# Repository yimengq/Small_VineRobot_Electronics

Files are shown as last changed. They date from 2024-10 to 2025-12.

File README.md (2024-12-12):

# Board Design for Vine Robot:

## Overview:
### Gen 1 Board:
- Initially split into 4 total boards, 2 on outside for Sensing board + Power Module, and 2 on inside for POE communication board
- The external tip sensing board is designed based on ESP32 XIAO

### Gen 2 Board:
-

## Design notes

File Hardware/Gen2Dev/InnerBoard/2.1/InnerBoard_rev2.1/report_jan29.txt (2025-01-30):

Info: Processing symbol 'C1:Capacitor_SMD:C_0805_2012Metric'.
Info: Processing symbol 'C2:Capacitor_SMD:C_0805_2012Metric'.
Info: Processing symbol 'C3:Capacitor_SMD:C_0805_2012Metric'.
Info: Processing symbol 'C4:Capacitor_SMD:C_0805_2012Metric'.
Info: Processing symbol 'C5:Capacitor_SMD:C_0805_2012Metric'.
Info: Processing symbol 'C6:Capacitor_SMD:C_0805_2012Metric'.
Info: Processing symbol 'C7:Capacitor_SMD:C_0805_2012Metric'.
Info: Processing symbol 'C8:Capacitor_SMD:C_0805_2012Metric'.
Info: Processing symbol 'C20:Capacitor_SMD:C_0805_2012Metric'.
Info: Processing symbol 'C21:Capacitor_SMD:C_0805_2012Metric'.
Info: Processing symbol 'C22:Capacitor_SMD:C_0805_2012Metric'.
Info: Processing symbol 'C23:Capacitor_SMD:C_0805_2012Metric'.
Info: Processing symbol 'C24:Capacitor_SMD:C_0402_1005Metric'.
Info: Processing symbol 'C25:Capacitor_SMD:C_0805_2012Metric'.
Info: Processing symbol 'C26:'.
Info: Processing symbol 'Y3:ASV-50.000MHZ-LCS-T:XTAL_ASV-50.000MHZ-LCS-T'.
Info: Processing symbol 'C27:'.
Info: Processing symbol 'Y1:ABLS2-12.000MHZ-D4Y-T:XTAL_ABLS2-12.000MHZ-D4Y-T'.
Info: Processing symbol 'C29:Capacitor_SMD:C_0402_1005Metric'.
Info: Processing symbol 'C31:Capacitor_SMD:C_0805_2012Metric'.
Info: Processing symbol 'C32:Capacitor_SMD:C_0805_2012Metric'.
Info: Processing symbol 'C59:Capacitor_SMD:C_0805_2012Metric'.
Info: Processing symbol 'C60:Capacitor_SMD:C_0805_2012Metric'.
Info: Processing symbol 'C61:Capacitor_SMD:C_0805_2012Metric'.
Info: Processing symbol 'C62:Capacitor_SMD:C_0805_2012Metric'.
Info: Processing symbol 'C63:Capacitor_SMD:C_0805_2012Metric'.
Info: Processing symbol 'C64:Capacitor_SMD:C_0805_2012Metric'.
Info: Processing symbol 'C65:Capacitor_SMD:C_0805_2012Metric'.
Info: Processing symbol 'C66:Capacitor_SMD:C_0805_2012Metric'.
Info: Processing symbol 'C67:Capacitor_SMD:C_0805_2012Metric'.
Info: Processing symbol 'C68:Capacitor_SMD:C_0805_2012Metric'.
Info: Processing symbol 'C69:Capacitor_SMD:C_0805_2012Metric'.
Info: Processing symbol 'C70:Capacitor_SMD:C_0805_2012Metric'.
Info: Processing symbol 'C71:Capacitor_SMD:C_0805_2012Metric'.
Info: Processing symbol 'C72:Capacitor_SMD:C_0805_2012Metric'.
Info: Processing symbol 'D4:LED_SMD:LED_0603_1608Metric'.
Info: Processing symbol 'D5:LED_SMD:LED_0603_1608Metric'.
Info: Processing symbol 'D6:Diode_THT:D_DO-41_SOD81_P10.16mm_Horizontal'.
Info: Processing symbol 'D7:LED_SMD:LED_0603_1608Metric'.
Info: Processing symbol 'D10:Diode_SMD:D_SOD-323'.
Info: Processing symbol 'D11:LED_SMD:LED_0603_1608Metric'.
Info: Processing symbol 'D13:Diode_SMD:D_SOD-323'.
Info: Processing symbol 'D14:Diode_SMD:D_SOD-323'.
Info: Processing symbol 'D15:Package_TO_SOT_SMD:SOT-23'.
Info: Processing symbol 'D23:Diode_SMD:D_SMA'.
Info: Processing symbol 'D24:Package_TO_SOT_SMD:SOT-23'.
Info: Processing symbol 'FID1:Fiducial:Fiducial_0.5mm_Mask1.5mm'.
Info: Processing symbol 'FID2:Fiducial:Fiducial_0.5mm_Mask1.5mm'.
Info: Processing symbol 'FID3:Fiducial:Fiducial_0.5mm_Mask1.5mm'.
Info: Processing symbol 'FID4:Fiducial:Fiducial_0.5mm_Mask1.5mm'.
Info: Processing symbol 'H1:MountingHole:MountingHole_2.1mm'.
Info: Processing symbol 'H2:MountingHole:MountingHole_2.1mm'.
Info: Processing symbol 'H3:MountingHole:MountingHole_2.1mm'.
Info: Processing symbol 'H4:MountingHole:MountingHole_2.1mm'.
Info: Processing symbol 'J1:HMTSW-102-X-X-S-X:SAMTEC_HMTSW-102-X-X-S-X'.
Info: Processing symbol 'U25:'.
Info: Processing symbol 'J2:HMTSW-102-X-X-S-X:SAMTEC_HMTSW-102-X-X-S-X'.
Info: Processing symbol 'J3:HMTSW-102-X-X-S-X:SAMTEC_HMTSW-102-X-X-S-X'.
Info: Processing symbol 'J4:HMTSW-102-X-X-S-X:SAMTEC_HMTSW-102-X-X-S-X'.
Info: Processing symbol 'J5:UJ31-CH-G2-SMT-TR:CUI_UJ31-CH-G2-SMT-TR'.
Info: Processing symbol 'J6:SI-46020-F:BEL_SI-46020-F'.
Info: Processing symbol 'U23:DBV0005A_N'.
Info: Processing symbol 'J7:HMTSW-102-X-X-S-X:SAMTEC_HMTSW-102-X-X-S-X'.
Info: Processing symbol 'U12:PW8'.
Info: Processing symbol 'J8:CONN10_3221-10-0300-00_CNC'.
Info: Processing symbol 'U11:QFN32_5X5MC_MCH'.
Info: Processing symbol 'J9:HMTSW-102-X-X-S-X:SAMTEC_HMTSW-102-X-X-S-X'.
Info: Processing symbol 'J10:HMTSW-102-X-X-S-X:SAMTEC_HMTSW-102-X-X-S-X'.
Info: Processing symbol 'U10:ESP32_WROOM_32E_N8:ESP32­WROOM­32E_EXP'.
Info: Processing symbol 'J11:HMTSW-102-X-X-S-X:SAMTEC_HMTSW-102-X-X-S-X'.
Info: Processing symbol 'U9:FT232RQ:QFN50P500X500X90-33N'.
Info: Processing symbol 'J12:HMTSW-102-X-X-S-X:SAMTEC_HMTSW-102-X-X-S-X'.
Info: Processing symbol 'U7:Package_TO_SOT_SMD:SOT-223-3_TabPin2'.
Info: Processing symbol 'J13:HMTSW-102-X-X-S-X:SAMTEC_HMTSW-102-X-X-S-X'.
Info: Processing symbol 'U6:Package_TO_SOT_SMD:SOT-23-5'.
Info: Processing symbol 'J14:HMTSW-102-X-X-S-X:SAMTEC_HMTSW-102-X-X-S-X'.
Info: Processing symbol 'U4:Package_TO_SOT_SMD:SOT-23-5'.
Info: Processing symbol 'J15:HMTSW-102-X-X-S-X:SAMTEC_HMTSW-102-X-X-S-X'.
Info: Processing symbol 'U1:DSS0012B'.
Info: Processing symbol 'J16:HMTSW-102-X-X-S-X:SAMTEC_HMTSW-102-X-X-S-X'.
Info: Processing symbol 'TP7:TestPoint:TestPoint_Pad_D2.0mm'.
Info: Processing symbol 'J17:HMTSW-102-X-X-S-X:SAMTEC_HMTSW-102-X-X-S-X'.
Info: Processing symbol 'TP6:TestPoint:TestPoint_Pad_D2.0mm'.
Info: Processing symbol 'J18:HMTSW-102-X-X-S-X:SAMTEC_HMTSW-102-X-X-S-X'.
Info: Processing symbol 'TP5:TestPoint:TestPoint_Pad_D2.0mm'.
Info: Processing symbol 'J19:HMTSW-102-X-X-S-X:SAMTEC_HMTSW-102-X-X-S-X'.
Info: Processing symbol 'TP4:TestPoint:TestPoint_Pad_D2.0mm'.
Info: Processing symbol 'JP1:'.
Info: Processing symbol 'TP3:TestPoint:TestPoint_Pad_D2.0mm'.
Info: Processing symbol 'L8:Inductor_SMD:L_0805_2012Metric'.
Info: Processing symbol 'L9:Inductor_SMD:L_0805_2012Metric'.
Info: Processing symbol 'MH1:OLIMEX_Other-FP:Mounting_hole_Shield_3.3mm'.
Info: Processing symbol 'TP2:TestPoint:TestPoint_Pad_D2.0mm'.
Info: Processing symbol 'MH2:OLIMEX_Other-FP:Mounting_hole_Shield_3.3mm'.
Info: Processing symbol 'TP1:TestPoint:TestPoint_Pad_D2.0mm'.
Info: Processing symbol 'Q1:SI2323DS-T1-GE3:SOT23'.
Info: Processing symbol 'Q4:Package_TO_SOT_SMD:SOT-23'.
Info: Processing symbol 'Q5:Package_TO_SOT_SMD:SOT-23'.
Info: Processing symbol 'Q9:SI2323DS-T1-GE3:SOT23'.
Info: Processing symbol 'Q10:Package_TO_SOT_SMD:SOT-23'.
Info: Processing symbol 'R1:Resistor_SMD:R_0805_2012Metric'.
Info: Processing symbol 'R2:Resistor_SMD:R_0805_2012Metric'.
Info: Processing symbol 'R3:Resistor_SMD:R_0805_2012Metric'.
Info: Processing symbol 'R4:Resistor_SMD:R_0805_2012Metric'.
Info: Processing symbol 'R5:Resistor_SMD:R_0805_2012Metric'.
Info: Processing symbol 'R6:Resistor_SMD:R_0805_2012Metric'.
Info: Processing symbol 'R7:Resistor_SMD:R_0805_2012Metric'.
Info: Processing symbol 'R8:Resistor_SMD:R_0805_2012Metric'.
Info: Processing symbol 'R21:Resistor_SMD:R_0805_2012Metric'.
Info: Processing symbol 'R22:Resistor_SMD:R_0805_2012Metric'.
Info: Processing symbol 'R23:Resistor_SMD:R_0805_2012Metric'.
Info: Processing symbol 'R24:Resistor_SMD:R_0805_2012Metric'.
Info: Processing symbol 'R25:Resistor_SMD:R_0805_2012Metric'.
Info: Processing symbol 'R26:Resistor_SMD:R_0805_2012Metric'.
Info: Processing symbol 'R27:Resistor_SMD:R_0805_2012Metric'.
Info: Processing symbol 'R28:Resistor_SMD:R_0805_2012Metric'.
Info: Processing symbol 'R29:Resistor_SMD:R_0805_2012Metric'.
Info: Processing symbol 'R30:Resistor_SMD:R_0805_2012Metric'.
Info: Processing symbol 'R31:Resistor_SMD:R_0805_2012Metric'.
Info: Processing symbol 'R32:Resistor_SMD:R_0805_2012Metric'.
Info: Processing symbol 'R33:Resistor_SMD:R_0805_2012Metric'.
Info: Processing symbol 'R34:Resistor_SMD:R_0805_2012Metric'.
Info: Processing symbol 'R35:Resistor_SMD:R_0805_2012Metric'.
Info: Processing symbol 'R41:Resistor_SMD:R_0805_2012Metric'.
Info: Processing symbol 'R42:Resistor_SMD:R_0805_2012Metric'.
Info: Processing symbol 'R43:Resistor_SMD:R_0805_2012Metric'.
Info: Processing symbol 'R45:Resistor_SMD:R_0805_2012Metric'.
Info: Processing symbol 'R46:Resistor_SMD:R_0805_2012Metric'.
Info: Processing symbol 'R47:Resistor_SMD:R_0805_2012Metric'.
Info: Processing symbol 'R49:Resistor_SMD:R_0805_2012Metric'.
Info: Processing symbol 'R50:Resistor_SMD:R_0805_2012Metric'.
Info: Processing symbol 'R51:Resistor_SMD:R_0805_2012Metric'.
Info: Processing symbol 'R52:Resistor_SMD:R_0805_2012Metric'.
Info: Processing symbol 'R81:Resistor_SMD:R_0805_2012Metric'.
Info: Processing symbol 'R82:Resistor_SMD:R_0805_2012Metric'.
Info: Processing symbol 'R83:Resistor_SMD:R_0805_2012Metric'.
Info: Processing symbol 'R84:Resistor_SMD:R_0805_2012Metric'.
Info: Processing symbol 'R89:Resistor_SMD:R_0805_2012Metric'.
Info: Processing symbol 'R90:Resistor_SMD:R_0805_2012Metric'.
Info: Processing symbol 'R93:Resistor_SMD:R_0805_2012Metric'.
Info: Processing symbol 'R94:Resistor_SMD:R_0805_2012Metric'.
Info: Processing symbol 'R97:Resistor_SMD:R_0805_2012Metric'.
Info: Processing symbol 'R99:Resistor_SMD:R_0805_2012Metric'.
Info: Processing symbol 'R100:Resistor_SMD:R_0805_2012Metric'.
Info: Processing symbol 'R101:Resistor_SMD:R_0805_2012Metric'.
Info: Processing symbol 'R104:Resistor_SMD:R_0805_2012Metric'.
Info: Processing symbol 'R105:Resistor_SMD:R_0805_2012Metric'.
Info: Processing symbol 'R106:Resistor_SMD:R_0805_2012Metric'.
Info: Processing symbol 'R107:Resistor_SMD:R_0805_2012Metric'.
Info: Processing symbol 'R108:Resistor_SMD:R_0805_2012Metric'.
Info: Processing symbol 'R109:Resistor_SMD:R_0805_2012Metric'.
Info: Processing symbol 'SW1:SW4_PTS815 SJM 250 SMTR LFS_CNK'.
Info: Processing symbol 'SW2:SW4_PTS815 SJM 250 SMTR LFS_CNK'.
Warning: No net found for component U9 pad 23 (no pin 23 in symbol).
Warning: No net found for component J6 pad 8 (no pin 8 in symbol).
Warning: No net found for component U9 pad 5 (no pin 5 in symbol).
Warning: No net found for component U9 pad 12 (no pin 12 in symbol).
Warning: No net found for component U9 pad 25 (no pin 25 in symbol).
Warning: No net found for component U9 pad 29 (no pin 29 in symbol).
Warning: No net found for component U9 pad 13 (no pin 13 in symbol).
Warning: No net found for component U6 pad 1 (no pin 1 in symbol).
Error: Cannot add J16 (footprint 'HMTSW-102-X-X-S-X:SAMTEC_HMTSW-102-X-X-S-X' not found).
Error: Cannot add J15 (footprint 'HMTSW-102-X-X-S-X:SAMTEC_HMTSW-102-X-X-S-X' not found).
Error: Cannot update U1 (footprint 'DSS0012B' not found).
Error: Cannot add J14 (footprint 'HMTSW-102-X-X-S-X:SAMTEC_HMTSW-102-X-X-S-X' not found).
Error: Cannot add J13 (footprint 'HMTSW-102-X-X-S-X:SAMTEC_HMTSW-102-X-X-S-X' not found).
Error: Cannot add J17 (footprint 'HMTSW-102-X-X-S-X:SAMTEC_HMTSW-102-X-X-S-X' not found).
Error: Cannot add J12 (footprint 'HMTSW-102-X-X-S-X:SAMTEC_HMTSW-102-X-X-S-X' not found).
Error: Cannot add J11 (footprint 'HMTSW-102-X-X-S-X:SAMTEC_HMTSW-102-X-X-S-X' not found).
Error: Cannot update SW1 (footprint 'SW4_PTS815 SJM 250 SMTR LFS_CNK' not found).
Error: Cannot add J18 (footprint 'HMTSW-102-X-X-S-X:SAMTEC_HMTSW-102-X-X-S-X' not found).
Error: Cannot add J19 (footprint 'HMTSW-102-X-X-S-X:SAMTEC_HMTSW-102-X-X-S-X' not found).
Error: Cannot add JP1 (no footprint assigned).
Error: Cannot add MH1 (footprint 'OLIMEX_Other-FP:Mounting_hole_Shield_3.3mm' not found).
Error: Cannot add MH2 (footprint 'OLIMEX_Other-FP:Mounting_hole_Shield_3.3mm' not found).
Error: Cannot add J10 (footprint 'HMTSW-102-X-X-S-X:SAMTEC_HMTSW-102-X-X-S-X' not found).
Error: Cannot update J8 (footprint 'CONN10_3221-10-0300-00_CNC' not found).
Error: Cannot update U11 (footprint 'QFN32_5X5MC_MCH' not found).
Error: Cannot add J7 (footprint 'HMTSW-102-X-X-S-X:SAMTEC_HMTSW-102-X-X-S-X' not found).
Error: Cannot update U12 (footprint 'PW8' not found).
Error: Cannot update SW2 (footprint 'SW4_PTS815 SJM 250 SMTR LFS_CNK' not found).
Error: Cannot update U23 (footprint 'DBV0005A_N' not found).
Error: Cannot add J1 (footprint 'HMTSW-102-X-X-S-X:SAMTEC_HMTSW-102-X-X-S-X' not found).
Error: Cannot add U25 (no footprint assigned).
Error: Cannot add C27 (no footprint assigned).
Error: Cannot add C26 (no footprint assigned).

Info: Total warnings: 8, errors: 25.

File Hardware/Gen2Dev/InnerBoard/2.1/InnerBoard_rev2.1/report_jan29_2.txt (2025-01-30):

Info: Processing symbol 'C1:Capacitor_SMD:C_0805_2012Metric'.
Info: Processing symbol 'C2:Capacitor_SMD:C_0805_2012Metric'.
Info: Processing symbol 'C3:Capacitor_SMD:C_0805_2012Metric'.
Info: Processing symbol 'C4:Capacitor_SMD:C_0805_2012Metric'.
Info: Processing symbol 'C5:Capacitor_SMD:C_0805_2012Metric'.
Info: Processing symbol 'C6:Capacitor_SMD:C_0805_2012Metric'.
Info: Processing symbol 'C7:Capacitor_SMD:C_0805_2012Metric'.
Info: Processing symbol 'C8:Capacitor_SMD:C_0805_2012Metric'.
Info: Processing symbol 'C20:Capacitor_SMD:C_0805_2012Metric'.
Info: Processing symbol 'C21:Capacitor_SMD:C_0805_2012Metric'.
Info: Processing symbol 'C22:Capacitor_SMD:C_0805_2012Metric'.
Info: Processing symbol 'C23:Capacitor_SMD:C_0805_2012Metric'.
Info: Processing symbol 'C24:Capacitor_SMD:C_0402_1005Metric'.
Info: Processing symbol 'C25:Capacitor_SMD:C_0805_2012Metric'.
Info: Processing symbol 'C26:'.
Info: Processing symbol 'Y1:ABLS2-12.000MHZ-D4Y-T:XTAL_ABLS2-12.000MHZ-D4Y-T'.
Info: Processing symbol 'C27:'.
Info: Processing symbol 'U25:'.
Info: Processing symbol 'C29:Capacitor_SMD:C_0402_1005Metric'.
Info: Processing symbol 'C31:Capacitor_SMD:C_0805_2012Metric'.
Info: Processing symbol 'C32:Capacitor_SMD:C_0805_2012Metric'.
Info: Processing symbol 'C59:Capacitor_SMD:C_0805_2012Metric'.
Info: Processing symbol 'C60:Capacitor_SMD:C_0805_2012Metric'.
Info: Processing symbol 'C61:Capacitor_SMD:C_0805_2012Metric'.
Info: Processing symbol 'C62:Capacitor_SMD:C_0805_2012Metric'.
Info: Processing symbol 'C63:Capacitor_SMD:C_0805_2012Metric'.
Info: Processing symbol 'C64:Capacitor_SMD:C_0805_2012Metric'.
Info: Processing symbol 'C65:Capacitor_SMD:C_0805_2012Metric'.
Info: Processing symbol 'C66:Capacitor_SMD:C_0805_2012Metric'.
Info: Processing symbol 'C67:Capacitor_SMD:C_0805_2012Metric'.
Info: Processing symbol 'C68:Capacitor_SMD:C_0805_2012Metric'.
Info: Processing symbol 'C69:Capacitor_SMD:C_0805_2012Metric'.
Info: Processing symbol 'C70:Capacitor_SMD:C_0805_2012Metric'.
Info: Processing symbol 'C71:Capacitor_SMD:C_0805_2012Metric'.
Info: Processing symbol 'C72:Capacitor_SMD:C_0805_2012Metric'.
Info: Processing symbol 'D4:LED_SMD:LED_0603_1608Metric'.
Info: Processing symbol 'D5:LED_SMD:LED_0603_1608Metric'.
Info: Processing symbol 'D6:Diode_THT:D_DO-41_SOD81_P10.16mm_Horizontal'.
Info: Processing symbol 'D7:LED_SMD:LED_0603_1608Metric'.
Info: Processing symbol 'D10:Diode_SMD:D_SOD-323'.
Info: Processing symbol 'D11:LED_SMD:LED_0603_1608Metric'.
Info: Processing symbol 'D13:Diode_SMD:D_SOD-323'.
Info: Processing symbol 'D14:Diode_SMD:D_SOD-323'.
Info: Processing symbol 'D15:Package_TO_SOT_SMD:SOT-23'.
Info: Processing symbol 'D23:Diode_SMD:D_SMA'.
Info: Processing symbol 'D24:Package_TO_SOT_SMD:SOT-23'.
Info: Processing symbol 'FID1:Fiducial:Fiducial_0.5mm_Mask1.5mm'.
Info: Processing symbol 'FID2:Fiducial:Fiducial_0.5mm_Mask1.5mm'.
Info: Processing symbol 'FID3:Fiducial:Fiducial_0.5mm_Mask1.5mm'.
Info: Processing symbol 'FID4:Fiducial:Fiducial_0.5mm_Mask1.5mm'.
Info: Processing symbol 'H1:MountingHole:MountingHole_2.1mm'.
Info: Processing symbol 'H2:MountingHole:MountingHole_2.1mm'.
Info: Processing symbol 'H3:MountingHole:MountingHole_2.1mm'.
Info: Processing symbol 'H4:MountingHole:MountingHole_2.1mm'.
Info: Processing symbol 'J1:HMTSW-102-X-X-S-X:SAMTEC_HMTSW-102-X-X-S-X'.
Info: Processing symbol 'U23:DBV0005A_N'.
Info: Processing symbol 'J2:HMTSW-102-X-X-S-X:SAMTEC_HMTSW-102-X-X-S-X'.
Info: Processing symbol 'J3:HMTSW-102-X-X-S-X:SAMTEC_HMTSW-102-X-X-S-X'.
Info: Processing symbol 'J4:HMTSW-102-X-X-S-X:SAMTEC_HMTSW-102-X-X-S-X'.
Info: Processing symbol 'J5:UJ31-CH-G2-SMT-TR:CUI_UJ31-CH-G2-SMT-TR'.
Info: Processing symbol 'J6:SI-46020-F:BEL_SI-46020-F'.
Info: Processing symbol 'U12:PW8'.
Info: Processing symbol 'J7:HMTSW-102-X-X-S-X:SAMTEC_HMTSW-102-X-X-S-X'.
Info: Processing symbol 'U11:QFN32_5X5MC_MCH'.
Info: Processing symbol 'J8:CONN10_3221-10-0300-00_CNC'.
Info: Processing symbol 'U10:ESP32_WROOM_32E_N8:ESP32­WROOM­32E_EXP'.
Info: Processing symbol 'J9:HMTSW-102-X-X-S-X:SAMTEC_HMTSW-102-X-X-S-X'.
Info: Processing symbol 'J10:HMTSW-102-X-X-S-X:SAMTEC_HMTSW-102-X-X-S-X'.
Info: Processing symbol 'U9:FT232RQ:QFN50P500X500X90-33N'.
Info: Processing symbol 'J11:HMTSW-102-X-X-S-X:SAMTEC_HMTSW-102-X-X-S-X'.
Info: Processing symbol 'U7:Package_TO_SOT_SMD:SOT-223-3_TabPin2'.
Info: Processing symbol 'J12:HMTSW-102-X-X-S-X:SAMTEC_HMTSW-102-X-X-S-X'.
Info: Processing symbol 'U6:Package_TO_SOT_SMD:SOT-23-5'.
Info: Processing symbol 'J13:HMTSW-102-X-X-S-X:SAMTEC_HMTSW-102-X-X-S-X'.
Info: Processing symbol 'U4:Package_TO_SOT_SMD:SOT-23-5'.
Info: Processing symbol 'J14:HMTSW-102-X-X-S-X:SAMTEC_HMTSW-102-X-X-S-X'.
Info: Processing symbol 'U1:DSS0012B'.
Info: Processing symbol 'J15:HMTSW-102-X-X-S-X:SAMTEC_HMTSW-102-X-X-S-X'.
Info: Processing symbol 'TP30:TestPoint:TestPoint_Pad_D2.0mm'.
Info: Processing symbol 'J16:HMTSW-102-X-X-S-X:SAMTEC_HMTSW-102-X-X-S-X'.
Info: Processing symbol 'TP29:TestPoint:TestPoint_Pad_D2.0mm'.
Info: Processing symbol 'J17:HMTSW-102-X-X-S-X:SAMTEC_HMTSW-102-X-X-S-X'.
Info: Processing symbol 'TP28:TestPoint:TestPoint_Pad_D2.0mm'.
Info: Processing symbol 'J18:HMTSW-102-X-X-S-X:SAMTEC_HMTSW-102-X-X-S-X'.
Info: Processing symbol 'TP27:TestPoint:TestPoint_Pad_D2.0mm'.
Info: Processing symbol 'J19:HMTSW-102-X-X-S-X:SAMTEC_HMTSW-102-X-X-S-X'.
Info: Processing symbol 'TP26:TestPoint:TestPoint_Pad_D2.0mm'.
Info: Processing symbol 'JP1:'.
Info: Processing symbol 'TP25:TestPoint:TestPoint_Pad_D2.0mm'.
Info: Processing symbol 'L8:Inductor_SMD:L_0805_2012Metric'.
Info: Processing symbol 'L9:Inductor_SMD:L_0805_2012Metric'.
Info: Processing symbol 'MH1:OLIMEX_Other-FP:Mounting_hole_Shield_3.3mm'.
Info: Processing symbol 'TP24:TestPoint:TestPoint_Pad_D2.0mm'.
Info: Processing symbol 'MH2:OLIMEX_Other-FP:Mounting_hole_Shield_3.3mm'.
Info: Processing symbol 'TP23:TestPoint:TestPoint_Pad_D2.0mm'.
Info: Processing symbol 'Q1:SI2323DS-T1-GE3:SOT23'.
Info: Processing symbol 'Q4:Package_TO_SOT_SMD:SOT-23'.
Info: Processing symbol 'Q5:Package_TO_SOT_SMD:SOT-23'.
Info: Processing symbol 'Q9:SI2323DS-T1-GE3:SOT23'.
Info: Processing symbol 'Q10:Package_TO_SOT_SMD:SOT-23'.
Info: Processing symbol 'R1:Resistor_SMD:R_0805_2012Metric'.
Info: Processing symbol 'R2:Resistor_SMD:R_0805_2012Metric'.
Info: Processing symbol 'R3:Resistor_SMD:R_0805_2012Metric'.
Info: Processing symbol 'R4:Resistor_SMD:R_0805_2012Metric'.
Info: Processing symbol 'R5:Resistor_SMD:R_0805_2012Metric'.
Info: Processing symbol 'R6:Resistor_SMD:R_0805_2012Metric'.
Info: Processing symbol 'R7:Resistor_SMD:R_0805_2012Metric'.
Info: Processing symbol 'R8:Resistor_SMD:R_0805_2012Metric'.
Info: Processing symbol 'R21:Resistor_SMD:R_0805_2012Metric'.
Info: Processing symbol 'R22:Resistor_SMD:R_0805_2012Metric'.
Info: Processing symbol 'R23:Resistor_SMD:R_0805_2012Metric'.
Info: Processing symbol 'R24:Resistor_SMD:R_0805_2012Metric'.
Info: Processing symbol 'R25:Resistor_SMD:R_0805_2012Metric'.
Info: Processing symbol 'R26:Resistor_SMD:R_0805_2012Metric'.
Info: Processing symbol 'R27:Resistor_SMD:R_0805_2012Metric'.
Info: Processing symbol 'R28:Resistor_SMD:R_0805_2012Metric'.
Info: Processing symbol 'R29:Resistor_SMD:R_0805_2012Metric'.
Info: Processing symbol 'R30:Resistor_SMD:R_0805_2012Metric'.
Info: Processing symbol 'R31:Resistor_SMD:R_0805_2012Metric'.
Info: Processing symbol 'R32:Resistor_SMD:R_0805_2012Metric'.
Info: Processing symbol 'R33:Resistor_SMD:R_0805_2012Metric'.
Info: Processing symbol 'R34:Resistor_SMD:R_0805_2012Metric'.
Info: Processing symbol 'R35:Resistor_SMD:R_0805_2012Metric'.
Info: Processing symbol 'R41:Resistor_SMD:R_0805_2012Metric'.
Info: Processing symbol 'R42:Resistor_SMD:R_0805_2012Metric'.
Info: Processing symbol 'R43:Resistor_SMD:R_0805_2012Metric'.
Info: Processing symbol 'R45:Resistor_SMD:R_0805_2012Metric'.
Info: Processing symbol 'R46:Resistor_SMD:R_0805_2012Metric'.
Info: Processing symbol 'R47:Resistor_SMD:R_0805_2012Metric'.
Info: Processing symbol 'R49:Resistor_SMD:R_0805_2012Metric'.
Info: Processing symbol 'R50:Resistor_SMD:R_0805_2012Metric'.
Info: Processing symbol 'R51:Resistor_SMD:R_0805_2012Metric'.
Info: Processing symbol 'R52:Resistor_SMD:R_0805_2012Metric'.
Info: Processing symbol 'R81:Resistor_SMD:R_0805_2012Metric'.
Info: Processing symbol 'R82:Resistor_SMD:R_0805_2012Metric'.
Info: Processing symbol 'R83:Resistor_SMD:R_0805_2012Metric'.
Info: Processing symbol 'R84:Resistor_SMD:R_0805_2012Metric'.
Info: Processing symbol 'R89:Resistor_SMD:R_0805_2012Metric'.
Info: Processing symbol 'R90:Resistor_SMD:R_0805_2012Metric'.
Info: Processing symbol 'R93:Resistor_SMD:R_0805_2012Metric'.
Info: Processing symbol 'R94:Resistor_SMD:R_0805_2012Metric'.
Info: Processing symbol 'R97:Resistor_SMD:R_0805_2012Metric'.
Info: Processing symbol 'R99:Resistor_SMD:R_0805_2012Metric'.
Info: Processing symbol 'R100:Resistor_SMD:R_0805_2012Metric'.
Info: Processing symbol 'R101:Resistor_SMD:R_0805_2012Metric'.
Info: Processing symbol 'R104:Resistor_SMD:R_0805_2012Metric'.
Info: Processing symbol 'R105:Resistor_SMD:R_0805_2012Metric'.
Info: Processing symbol 'R106:Resistor_SMD:R_0805_2012Metric'.
Info: Processing symbol 'R107:Resistor_SMD:R_0805_2012Metric'.
Info: Processing symbol 'R108:Resistor_SMD:R_0805_2012Metric'.
Info: Processing symbol 'R109:Resistor_SMD:R_0805_2012Metric'.
Info: Processing symbol 'SW1:SW4_PTS815 SJM 250 SMTR LFS_CNK'.
Info: Processing symbol 'TP22:TestPoint:TestPoint_Pad_D2.0mm'.
Info: Processing symbol 'SW2:SW4_PTS815 SJM 250 SMTR LFS_CNK'.
Info: Processing symbol 'TP21:TestPoint:TestPoint_Pad_D2.0mm'.
Info: Processing symbol 'TP1:TestPoint:TestPoint_Pad_D2.0mm'.
Info: Processing symbol 'TP2:TestPoint:TestPoint_Pad_D2.0mm'.
Info: Processing symbol 'TP3:TestPoint:TestPoint_Pad_D2.0mm'.
Info: Processing symbol 'TP4:TestPoint:TestPoint_Pad_D2.0mm'.
Info: Processing symbol 'TP5:TestPoint:TestPoint_Pad_D2.0mm'.
Info: Processing symbol 'TP6:TestPoint:TestPoint_Pad_D2.0mm'.
Info: Processing symbol 'TP8:TestPoint:TestPoint_Pad_D2.0mm'.
Info: Processing symbol 'TP20:TestPoint:TestPoint_Pad_D2.0mm'.
Info: Processing symbol 'TP19:TestPoint:TestPoint_Pad_D2.0mm'.
Info: Processing symbol 'TP18:TestPoint:TestPoint_Pad_D2.0mm'.
Info: Processing symbol 'TP17:TestPoint:TestPoint_Pad_D2.0mm'.
Info: Processing symbol 'TP16:TestPoint:TestPoint_Pad_D2.0mm'.
Info: Processing symbol 'TP15:TestPoint:TestPoint_Pad_D2.0mm'.
Info: Processing symbol 'TP14:TestPoint:TestPoint_Pad_D2.0mm'.
Info: Processing symbol 'TP13:TestPoint:TestPoint_Pad_D2.0mm'.
Info: Processing symbol 'Y3:ASV-50.000MHZ-LCS-T:XTAL_ASV-50.000MHZ-LCS-T'.
Info: Processing symbol 'TP9:TestPoint:TestPoint_Pad_D2.0mm'.
Info: Processing symbol 'TP12:TestPoint:TestPoint_Pad_D2.0mm'.
Info: Processing symbol 'TP11:TestPoint:TestPoint_Pad_D2.0mm'.
Info: Processing symbol 'TP10:TestPoint:TestPoint_Pad_D2.0mm'.
Updated TP9 symbol association from  to /6baada33-aa96-4fe6-9113-43f1f558f684.
Updated TP9 sheetname to 'Root'.
Updated TP9 sheetfile to 'InnerBoard_rev2.1.kicad_sch'.
Updated TP9 footprint filters to 'Pin* Test*'.
Removed TP9 'exclude from BOM' fabrication attribute.
Connected TP9 pin 1 to Net-(C71-Pad2).
Changed TP9 value from TestPoint_Pad_D2.0mm to TestPoint.
Added TP10 (footprint 'TestPoint:TestPoint_Pad_D2.0mm').
Changed REF** reference designator to TP10.
Changed TP10 value from TestPoint_Pad_D2.0mm to TestPoint.
Updated TP10 symbol association from  to /1567f1c0-5a2b-43b6-96a9-7105be66c10c.
Updated TP10 sheetname to 'Root'.
Updated TP10 sheetfile to 'InnerBoard_rev2.1.kicad_sch'.
Updated TP10 footprint filters to 'Pin* Test*'.
Removed TP10 'exclude from BOM' fabrication attribute.
Connected TP10 pin 1 to Spare2.
Changed REF** reference designator to TP9.
Added TP11 (footprint 'TestPoint:TestPoint_Pad_D2.0mm').
Changed REF** reference designator to TP11.
Changed TP11 value from TestPoint_Pad_D2.0mm to TestPoint.
Updated TP11 symbol association from  to /7062de12-79e4-4118-8f8d-67129581fe5f.
Updated TP11 sheetname to 'Root'.
Updated TP11 sheetfile to 'InnerBoard_rev2.1.kicad_sch'.
Updated TP11 footprint filters to 'Pin* Test*'.
Removed TP11 'exclude from BOM' fabrication attribute.
Connected TP11 pin 1 to Spare1.
Added TP9 (footprint 'TestPoint:TestPoint_Pad_D2.0mm').
Added TP12 (footprint 'TestPoint:TestPoint_Pad_D2.0mm').
Changed REF** reference designator to TP12.
Changed TP12 value from TestPoint_Pad_D2.0mm to TestPoint.
Updated TP12 symbol association from  to /c7cb2f0c-1bdc-45d0-a05b-4f7ba0fc8c7b.
Updated TP12 sheetname to 'Root'.
Connected TP8 pin 1 to OSC_DIS.
Updated TP12 footprint filters to 'Pin* Test*'.
Removed TP12 'exclude from BOM' fabrication attribute.
Connected TP12 pin 1 to Net-(U11-EPAD).
Removed TP8 'exclude from BOM' fabrication attribute.
Added TP13 (footprint 'TestPoint:TestPoint_Pad_D2.0mm').
Changed REF** reference designator to TP13.
Changed TP13 value from TestPoint_Pad_D2.0mm to TestPoint.
Updated TP13 symbol association from  to /bcef1eed-9b2b-4c54-8e5d-db2f056f6c87.
Updated TP13 sheetname to 'Root'.
Updated TP13 sheetfile to 'InnerBoard_rev2.1.kicad_sch'.
Updated TP13 footprint filters to 'Pin* Test*'.
Removed TP13 'exclude from BOM' fabrication attribute.
Connected TP13 pin 1 to D_Com.
Updated TP8 footprint filters to 'Pin* Test*'.
Added TP14 (footprint 'TestPoint:TestPoint_Pad_D2.0mm').
Changed REF** reference designator to TP14.
Changed TP14 value from TestPoint_Pad_D2.0mm to TestPoint.
Updated TP14 symbol association from  to /e5ea63ed-f4e0-403f-a414-85737eb8aaad.
Updated TP14 sheetname to 'Root'.
Updated TP14 sheetfile to 'InnerBoard_rev2.1.kicad_sch'.
Updated TP14 footprint filters to 'Pin* Test*'.
Removed TP14 'exclude from BOM' fabrication attribute.
Connected TP14 pin 1 to VDDA1/2.
Updated TP8 sheetfile to 'InnerBoard_rev2.1.kicad_sch'.
Added TP15 (footprint 'TestPoint:TestPoint_Pad_D2.0mm').
Changed REF** reference designator to TP15.
Changed TP15 value from TestPoint_Pad_D2.0mm to TestPoint.
Updated TP15 symbol association from  to /d527ba62-d9ac-45c6-8199-df9451cb6658.
Updated TP15 sheetname to 'Root'.
Updated TP15 sheetfile to 'InnerBoard_rev2.1.kicad_sch'.
Updated TP15 footprint filters to 'Pin* Test*'.
Removed TP15 'exclude from BOM' fabrication attribute.
Connected TP15 pin 1 to ESP_EN.
Updated TP8 sheetname to 'Root'.
Added TP16 (footprint 'TestPoint:TestPoint_Pad_D2.0mm').
Changed REF** reference designator to TP16.
Changed TP16 value from TestPoint_Pad_D2.0mm to TestPoint.
Updated TP16 symbol association from  to /d1f3ed2d-daec-4c6f-8942-47c1e0745468.
Updated TP16 sheetname to 'Root'.
Updated TP16 sheetfile to 'InnerBoard_rev2.1.kicad_sch'.
Updated TP16 footprint filters to 'Pin* Test*'.
Removed TP16 'exclude from BOM' fabrication attribute.
Connected TP16 pin 1 to +3.3VLAN.
Updated TP8 symbol association from  to /023d3b54-558e-41d1-8a4c-ee0ba2b6aaef.
Added TP17 (footprint 'TestPoint:TestPoint_Pad_D2.0mm').
Changed REF** reference designator to TP17.
Changed TP17 value from TestPoint_Pad_D2.0mm to TestPoint.
Updated TP17 symbol association from  to /6c0a5c35-ba72-4d07-862e-1288580fff16.
Updated TP17 sheetname to 'Root'.
Updated TP17 sheetfile to 'InnerBoard_rev2.1.kicad_sch'.
Updated TP17 footprint filters to 'Pin* Test*'.
Removed TP17 'exclude from BOM' fabrication attribute.
Connected TP17 pin 1 to Spare2.
Changed TP8 value from TestPoint_Pad_D2.0mm to TestPoint.
Added TP18 (footprint 'TestPoint:TestPoint_Pad_D2.0mm').
Changed REF** reference designator to TP18.
Changed TP18 value from TestPoint_Pad_D2.0mm to TestPoint.
Updated TP18 symbol association from  to /b75fff0e-efaa-4a0c-94cb-2920aa34688c.
Updated TP18 sheetname to 'Root'.
Updated TP18 sheetfile to 'InnerBoard_rev2.1.kicad_sch'.
Updated TP18 footprint filters to 'Pin* Test*'.
Removed TP18 'exclude from BOM' fabrication attribute.
Connected TP18 pin 1 to Net-(U12-UVLO).
Changed REF** reference designator to TP8.
Added TP19 (footprint 'TestPoint:TestPoint_Pad_D2.0mm').
Changed REF** reference designator to TP19.
Changed TP19 value from TestPoint_Pad_D2.0mm to TestPoint.
Updated TP19 symbol association from  to /e3ad6083-1446-41eb-9340-d69c70b52fe2.
Updated TP19 sheetname to 'Root'.
Updated TP19 sheetfile to 'InnerBoard_rev2.1.kicad_sch'.
Updated TP19 footprint filters to 'Pin* Test*'.
Removed TP19 'exclude from BOM' fabrication attribute.
Connected TP19 pin 1 to +5VP.
Added TP8 (footprint 'TestPoint:TestPoint_Pad_D2.0mm').
Added TP20 (footprint 'TestPoint:TestPoint_Pad_D2.0mm').
Changed REF** reference designator to TP20.
Changed TP20 value from TestPoint_Pad_D2.0mm to TestPoint.
Updated TP20 symbol association from  to /f5299f5d-6878-4394-902a-5c750fa8e632.
Updated TP20 sheetname to 'Root'.
Updated TP20 sheetfile to 'InnerBoard_rev2.1.kicad_sch'.
Updated TP20 footprint filters to 'Pin* Test*'.
Removed TP20 'exclude from BOM' fabrication attribute.
Connected TP20 pin 1 to VBUS.
Updated TP12 sheetfile to 'InnerBoard_rev2.1.kicad_sch'.
Added TP21 (footprint 'TestPoint:TestPoint_Pad_D2.0mm').
Changed REF** reference designator to TP21.
Changed TP21 value from TestPoint_Pad_D2.0mm to TestPoint.
Updated TP21 symbol association from  to /23b50038-7e48-425d-869d-8ebaa74cc40e.
Updated TP21 sheetname to 'Root'.
Updated TP21 sheetfile to 'InnerBoard_rev2.1.kicad_sch'.
Updated TP21 footprint filters to 'Pin* Test*'.
Removed TP21 'exclude from BOM' fabrication attribute.
Connected TP21 pin 1 to +5V.
Connected TP30 pin 1 to GPIO5/SPI_CS.
Added TP22 (footprint 'TestPoint:TestPoint_Pad_D2.0mm').
Changed REF** reference designator to TP22.
Changed TP22 value from TestPoint_Pad_D2.0mm to TestPoint.
Updated TP22 symbol association from  to /d2a7ec64-73a1-4d8d-a047-477f0932a324.
Updated TP22 sheetname to 'Root'.
Updated TP22 sheetfile to 'InnerBoard_rev2.1.kicad_sch'.
Updated TP22 footprint filters to 'Pin* Test*'.
Removed TP22 'exclude from BOM' fabrication attribute.
Connected TP22 pin 1 to +9V.
Removed TP30 'exclude from BOM' fabrication attribute.
Added TP23 (footprint 'TestPoint:TestPoint_Pad_D2.0mm').
Changed REF** reference designator to TP23.
Changed TP23 value from TestPoint_Pad_D2.0mm to TestPoint.
Updated TP23 symbol association from  to /2898ca49-4c4a-4b33-8b86-257164c50673.
Updated TP23 sheetname to 'Root'.
Updated TP23 sheetfile to 'InnerBoard_rev2.1.kicad_sch'.
Updated TP23 footprint filters to 'Pin* Test*'.
Removed TP23 'exclude from BOM' fabrication attribute.
Connected TP23 pin 1 to +3.3V.
Updated TP30 footprint filters to 'Pin* Test*'.
Added TP24 (footprint 'TestPoint:TestPoint_Pad_D2.0mm').
Changed REF** reference designator to TP24.
Changed TP24 value from TestPoint_Pad_D2.0mm to TestPoint.
Updated TP24 symbol association from  to /db690d6d-3832-4922-8787-71b01d960507.
Updated TP24 sheetname to 'Root'.
Updated TP24 sheetfile to 'InnerBoard_rev2.1.kicad_sch'.
Updated TP24 footprint filters to 'Pin* Test*'.
Removed TP24 'exclude from BOM' fabrication attribute.
Connected TP24 pin 1 to RMIISEL.
Updated TP30 sheetfile to 'InnerBoard_rev2.1.kicad_sch'.
Added TP25 (footprint 'TestPoint:TestPoint_Pad_D2.0mm').
Changed REF** reference designator to TP25.
Changed TP25 value from TestPoint_Pad_D2.0mm to TestPoint.
Updated TP25 symbol association from  to /ea5cd51e-44af-4205-83e0-52a23ab58acc.
Updated TP25 sheetname to 'Root'.
Updated TP25 sheetfile to 'InnerBoard_rev2.1.kicad_sch'.
Updated TP25 footprint filters to 'Pin* Test*'.
Removed TP25 'exclude from BOM' fabrication attribute.
Connected TP25 pin 1 to Net-(U25-VDD).
Updated TP30 sheetname to 'Root'.
Added TP26 (footprint 'TestPoint:TestPoint_Pad_D2.0mm').
Changed REF** reference designator to TP26.
Changed TP26 value from TestPoint_Pad_D2.0mm to TestPoint.
Updated TP26 symbol association from  to /f6c930f7-10bf-4e56-a248-4fd9497e862e.
Updated TP26 sheetname to 'Root'.
Updated TP26 sheetfile to 'InnerBoard_rev2.1.kicad_sch'.
Updated TP26 footprint filters to 'Pin* Test*'.
Removed TP26 'exclude from BOM' fabrication attribute.
Connected TP26 pin 1 to GPIO12/PHY_PWR.
Updated TP30 symbol association from  to /597af5c2-880d-4a95-b62b-8e9e5aa765af.
Added TP27 (footprint 'TestPoint:TestPoint_Pad_D2.0mm').
Changed REF** reference designator to TP27.
Changed TP27 value from TestPoint_Pad_D2.0mm to TestPoint.
Updated TP27 symbol association from  to /2d84ceed-f113-43e0-9ed7-c3a5eb137c14.
Updated TP27 sheetname to 'Root'.
Updated TP27 sheetfile to 'InnerBoard_rev2.1.kicad_sch'.
Updated TP27 footprint filters to 'Pin* Test*'.
Removed TP27 'exclude from BOM' fabrication attribute.
Connected TP27 pin 1 to GPIO15/HS2_CMD.
Changed TP30 value from TestPoint_Pad_D2.0mm to TestPoint.
Added TP28 (footprint 'TestPoint:TestPoint_Pad_D2.0mm').
Changed REF** reference designator to TP28.
Changed TP28 value from TestPoint_Pad_D2.0mm to TestPoint.
Updated TP28 symbol association from  to /e172e45f-28b6-43ed-a104-899f7bb8fd20.
Updated TP28 sheetname to 'Root'.
Updated TP28 sheetfile to 'InnerBoard_rev2.1.kicad_sch'.
Updated TP28 footprint filters to 'Pin* Test*'.
Removed TP28 'exclude from BOM' fabrication attribute.
Connected TP28 pin 1 to GPIO2/HS2_DATA0.
Changed REF** reference designator to TP30.
Added TP29 (footprint 'TestPoint:TestPoint_Pad_D2.0mm').
Changed REF** reference designator to TP29.
Changed TP29 value from TestPoint_Pad_D2.0mm to TestPoint.
Updated TP29 symbol association from  to /03b79476-c9ff-44dc-b22a-21540050c368.
Updated TP29 sheetname to 'Root'.
Updated TP29 sheetfile to 'InnerBoard_rev2.1.kicad_sch'.
Updated TP29 footprint filters to 'Pin* Test*'.
Removed TP29 'exclude from BOM' fabrication attribute.
Connected TP29 pin 1 to GPIO0.
Added TP30 (footprint 'TestPoint:TestPoint_Pad_D2.0mm').
Warning: No net found for component U9 pad 23 (no pin 23 in symbol).
Warning: No net found for component J6 pad 8 (no pin 8 in symbol).
Warning: No net found for component U9 pad 5 (no pin 5 in symbol).
Warning: No net found for component U9 pad 12 (no pin 12 in symbol).
Warning: No net found for component U9 pad 25 (no pin 25 in symbol).
Warning: No net found for component U9 pad 29 (no pin 29 in symbol).
Warning: No net found for component U9 pad 13 (no pin 13 in symbol).
Warning: No net found for component U6 pad 1 (no pin 1 in symbol).
Error: Cannot update SW1 (footprint 'SW4_PTS815 SJM 250 SMTR LFS_CNK' not found).
Error: Cannot add J14 (footprint 'HMTSW-102-X-X-S-X:SAMTEC_HMTSW-102-X-X-S-X' not found).
Error: Cannot update U1 (footprint 'DSS0012B' not found).
Error: Cannot add J13 (footprint 'HMTSW-102-X-X-S-X:SAMTEC_HMTSW-102-X-X-S-X' not found).
Error: Cannot add J12 (footprint 'HMTSW-102-X-X-S-X:SAMTEC_HMTSW-102-X-X-S-X' not found).
Error: Cannot add MH2 (footprint 'OLIMEX_Other-FP:Mounting_hole_Shield_3.3mm' not found).
Error: Cannot add J11 (footprint 'HMTSW-102-X-X-S-X:SAMTEC_HMTSW-102-X-X-S-X' not found).
Error: Cannot add J10 (footprint 'HMTSW-102-X-X-S-X:SAMTEC_HMTSW-102-X-X-S-X' not found).
Error: Cannot add J15 (footprint 'HMTSW-102-X-X-S-X:SAMTEC_HMTSW-102-X-X-S-X' not found).
Error: Cannot add MH1 (footprint 'OLIMEX_Other-FP:Mounting_hole_Shield_3.3mm' not found).
Error: Cannot add JP1 (no footprint assigned).
Error: Cannot add J19 (footprint 'HMTSW-102-X-X-S-X:SAMTEC_HMTSW-102-X-X-S-X' not found).
Error: Cannot add J18 (footprint 'HMTSW-102-X-X-S-X:SAMTEC_HMTSW-102-X-X-S-X' not found).
Error: Cannot add J17 (footprint 'HMTSW-102-X-X-S-X:SAMTEC_HMTSW-102-X-X-S-X' not found).
Error: Cannot update J8 (footprint 'CONN10_3221-10-0300-00_CNC' not found).
Error: Cannot add J7 (footprint 'HMTSW-102-X-X-S-X:SAMTEC_HMTSW-102-X-X-S-X' not found).
Error: Cannot update U11 (footprint 'QFN32_5X5MC_MCH' not found).
Error: Cannot add J16 (footprint 'HMTSW-102-X-X-S-X:SAMTEC_HMTSW-102-X-X-S-X' not found).
Error: Cannot update U12 (footprint 'PW8' not found).
Error: Cannot add J1 (footprint 'HMTSW-102-X-X-S-X:SAMTEC_HMTSW-102-X-X-S-X' not found).
Error: Cannot update U23 (footprint 'DBV0005A_N' not found).
Error: Cannot add C27 (no footprint assigned).
Error: Cannot add U25 (no footprint assigned).
Error: Cannot add C26 (no footprint assigned).
Error: Cannot update SW2 (footprint 'SW4_PTS815 SJM 250 SMTR LFS_CNK' not found).

Info: Total warnings: 8, errors: 25.

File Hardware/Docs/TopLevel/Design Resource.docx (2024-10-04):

Electronics System Outside

1. Power
  a. Lipo battery
    i. Feature
      1. Multiple cells connected in series.
      2. Current Requirements
        a. Continuous: [Enter value]
        b. Peak: [Enter value] +150mA (motor)
        c. Battery Operating Time: [Enter value]
    ii. Resources
      1. Purchase (https://nassaunationalcable.com/collections/grepow-lipo-round-shaped-batteries/products/grepow-580mah-3-7v-lipo-round-shaped-battery-5535035)
      2. Datasheet
  b. Voltage Converter
    i. Feature
      1. An IC convert voltage from 7.4V to 3.7V
  c. Protection Circuit
    i. Feature
      1. Reverse Polarity Protection
      2. Decoupling Capactiros
      3. EMI/ESD Protection
2. Micros + Sensor Peripheral
  a. ESP32-S3 (XIAO Seeed Studio)
    i. Resource
      1. Dev Board Purchase (https://www.amazon.com/Seeed-Studio-XIAO-ESP32C3-Microcontroller/dp/B0B94JZ2YF?sp_csd=d2lkZ2V0TmFtZT1zcF9hdGY)
      2. Schematic (https://github.com/yimengq/Small_VineRobot_Electronics/tree/main/Example_Schematics/XIAO%20Seeed%20Studio)
      3. Github (https://github.com/yimengq/Small_VineRobot_Electronics/tree/main/Example_Schematics/XIAO%20Seeed%20Studio)
      4. Official Website (https://wiki.seeedstudio.com/xiao_esp32s3_getting_started/)
  b. OV2640
  c. BNO055
    i. Feature: This is 9-axis IMU reused from Adafruit product
    ii. Resource
      1. Dev Board Purchase (https://www.adafruit.com/product/2472)
      2. Schematic (https://learn.adafruit.com/adafruit-bno055-absolute-orientation-sensor/downloads)
      3. Github (https://github.com/yimengq/Small_VineRobot_Electronics/tree/main/Example_Schematics/BNO055)

Electronics System Inside

1. Power
  a. ESP-PoE
    i. Feature
      1. 48V/30W,60W,90W
      2. Ethernet for data communication
    ii. Resources
      1. Dev Board Purchase (https://www.olimex.com/Products/IoT/ESP32/ESP32-POE/open-source-hardware)
      2. Schematic (https://github.com/yimengq/Small_VineRobot_Electronics/blob/main/Example_Schematics/ESP32_POE/Oilmex%20Board/ESP32-PoE_Rev_L1.pdf)
      3. Github (https://github.com/yimengq/Small_VineRobot_Electronics/tree/main/Example_Schematics/ESP32_POE/Oilmex%20Board)
2. Micros
  a. ESP32-WROOM

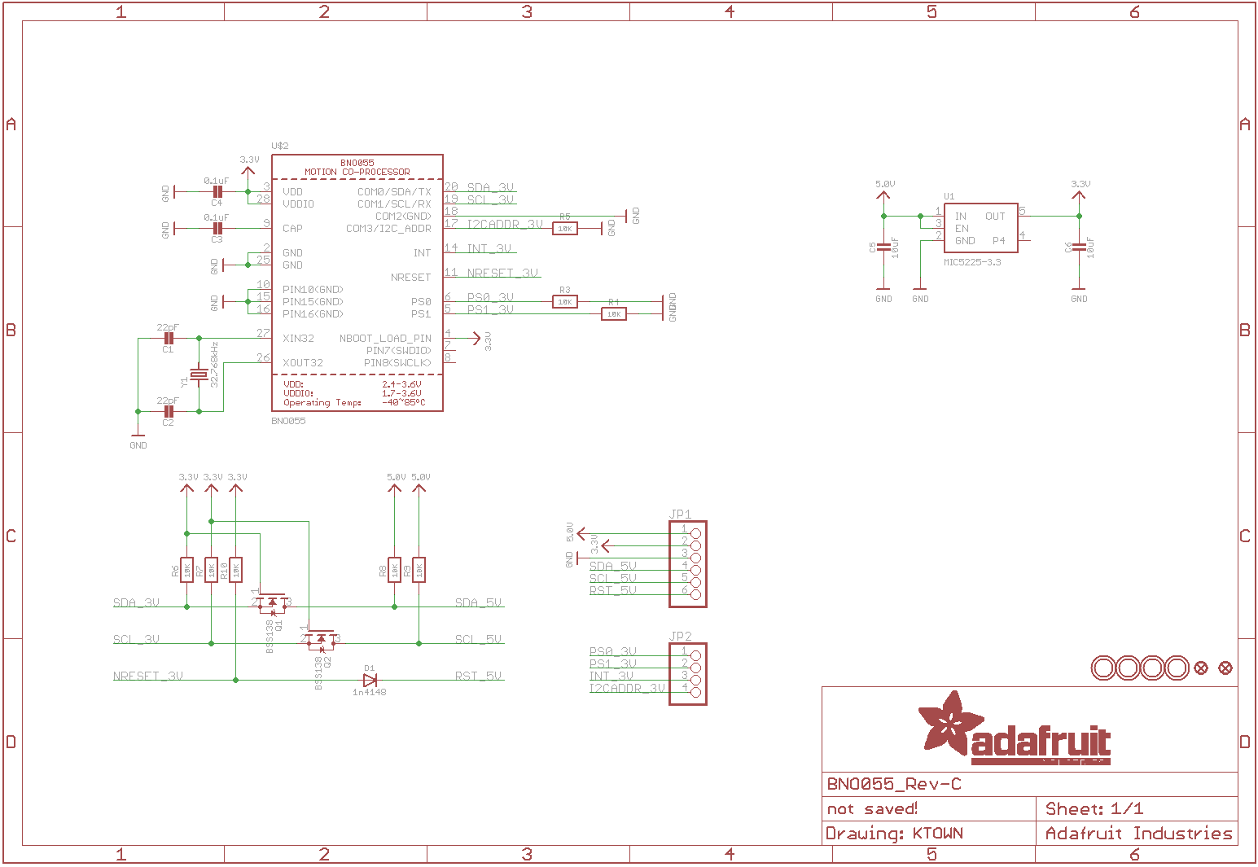
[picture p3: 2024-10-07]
Hardware/Example_Schematics/BNO055/sensors_BNO055_REV-C.png

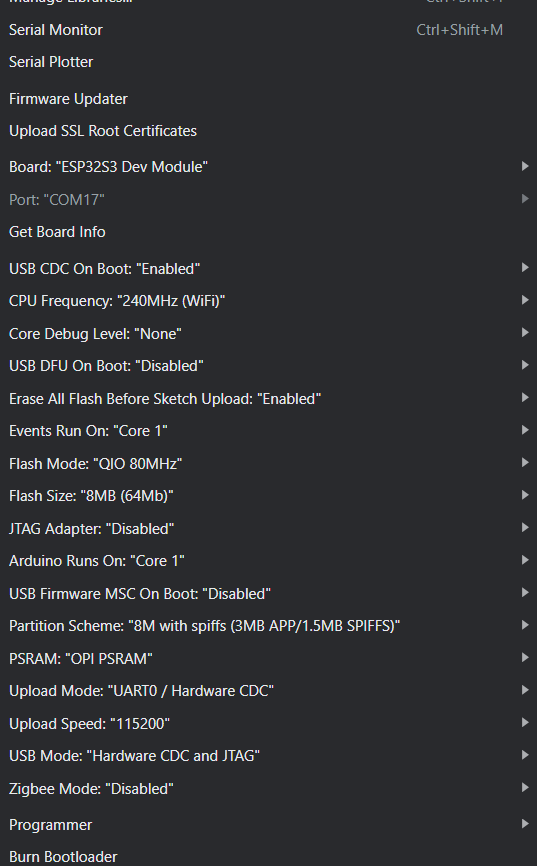
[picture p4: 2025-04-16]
Software/arduino_settings.png

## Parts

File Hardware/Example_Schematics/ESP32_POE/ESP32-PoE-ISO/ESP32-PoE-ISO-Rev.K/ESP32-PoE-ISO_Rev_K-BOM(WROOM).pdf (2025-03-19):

ESP32-PoE-ISO_Rev_K-BOM(WROOM) | 07/29/2022
Quantity | Designation | Package | Designator
1 | 0.03R/1%/R1206 | R1206 | R28
1 | 4.7R/R0402 | R0402 | R33
1 | 10R/R0402 | R0402 | R40
4 | 49.9R/1%/R0402 | R0402 | R10,R11,R12,R13
3 | 220R/R0402 | R0402 | R24,R46,R47
3 | 1k/R0402 | R0402 | R3,R20,R21
6 | 2.2k/R0402 | R0402 | R5,R8,R14,R15,R31,R35
3 | RA1206_(4X0603)_4B8_2.2k | R1206 | RM1,RM2,RM3
1 | 4.42k/1%/1/16W/R0402 | R0402 | R27
1 | 4.7k/R2512 | R2512 | R41
12 | 10k/R0402 | R0402 | R1,R2,R6,R18,R19,R25, R32,R36,R37,R39,R44,R48
1 | 10.5k/1%/R0402 | R0402 | R34
1 | 12.1k/1%/R0402 | R0402 | R26
1 | 24.9k/1%/R0402 | R0402 | R22
1 | 47k/R0402 | R0402 | R4
1 | 49.9k/1%/R0402 | R0402 | R30
1 | 56.2k/1%/R0402 | R0402 | R38
1 | 100k/R0402 | R0402 | R9
1 | 130k/R0402 | R0402 | R43
1 | 180k/1%/R0402 | R0402 | R23
1 | 220k/R0402 | R0402 | R29
2 | 470k/R0402 | R0402 | R7,R16
3 | FB0805/600R/2A | L0805 | L1,L3,L5
1 | 2.2uH/1.5A/DCR=72mR/ 20%/3.00x3.00x1.50mm/ CD32(NR3015T2R2M) | CD32 | L2
1 | 33uH/2.1A/DCR=0.1R/20%/ DBS135(PD3316MT330) | DBS135 | L4
1 | 12pF/50V/5%/COG/C0402 | C0402 | C25
2 | 27pF/50V/5%/C0G/C0402 | C0402 | C4,C5
1 | 1nF/50V/10%/X7R/C0402 | C0402 | C28
1 | 1nF/2000V/10%/X7R/C1206 | C1206 | C2
1 | 1.0nF/3kV/10%/X7R/SMD/1808 (VISHAY-VJ1808Y102KBHAT4X_ Farnell-2407291) | C1808 | C23
6 | 100nF/16V/10%/X7R/C0402 | C0402 | C8,C11,C14,C15, C16,C18
2 | 100nF/100V/10%/X7R/C0603 | C0603 | C12,C24
1 | 1uF/10V/20%/X5R/C0603 | C0603 | C31
1 | 2.2uF/6.3V/10%/X5R/C0603 | C0603 | C17
1 | 15uF/100V/20%/RM2.5/6.3x11mm (Farnell:1281844) | CPOL-RM2.5mm_ 6.3x11mm_PTH | C27
8 | 22uF/6.3V/20%/X5R/C0603 | C0603 | C1,C6,C7,C9,C10, C13,C19,C22
1 | 47uF/6.3V/20%/X5R/C0805 | C_0805_5MIL_DWS | C3
1 | 470uF/10V/20%/Low_ESR/ RM2.5/6.0x11mm | CPOL-RM2.5mm_ 6.3x11mm_PTH | C26
1 | BAT54C(SOT23-3) | SOT23-3 | D2
6 | 1N5819S4/SOD123 | SOD-123 | D1,D3,D4,D6,D7,D9
1 | ESDS314DBVR(SOT-23-5) | SOT-23-5 | TVS1
1 | SMAJ58A/SMA | SMA-KA | D10

ESP32-PoE-ISO_Rev_K-BOM(WROOM) | 07/29/2022
1 | SS510/100V/5A/0.85V/ DO214AB(SMC) | DO214AB(SMC) | D5
1 | LED/RED/0603 | LED0603 | PWR1
1 | LED/GREEN/0603 | LED0603 | LNK1
2 | LED/YELLOW/0603 | LED0603 | ACT1,CHRG1
2 | BC817-40(SOT23) | SOT23 | Q2,Q3
1 | LMUN2211LT1G(SOT-23) | SOT23 | T1
3 | WPM2015-3/TR | SOT23 | FET1,FET2,FET3
1 | BL4054B-42TPRN(SOT23-5) | SOT-23-5 | U3
1 | CH340T(SSOP20W) | SSOP-20W | U1
1 | ESP32-WROOM-32E | ESP32-WROVER(WROOM)-UNIVERSAL_MODULE | U6
1 | F0505S-2WR2(SIP-7) | SIP-7_Universal | DCDC1
1 | LAN8710A-EZC(QFN32) | QFN32 | U4
1 | SY8089AAAC(SOT23-5) | SOT-23-5 | U7
1 | Q12MHz/20pF/10ppm/4P/3.2x2.5mm | TSX-3.2x2.5mm | Q1
1 | TPS2376PW(TSSOP-8) | TSSOP-8 | U2
1 | TX4138(ESOIC-8) | ESOIC-8 | U5
2 | IT1185AU2 | IT1185AU2 | BUT1,RST1
1 | DW02S | DW02S | BAT1
1 | MISB-SWMM-5B-LF(USB_MICRO) | MISB-SWMM-5B_LF | USB-UART1
1 | P-B-V-10-LF | GBH-254-SMT-10 | UEXT1
1 | RJP-003TC1(LPJ4112CNL) | RJP-003TC1(LPJ4112CNL) | LAN_CON1
1 | TFC-9P-1.7H(ATFFS150A01BR016) | uSD(TFC-9P-1.xH (ATFFS150A01BR016)) | MICRO_SD1
2 | NA/R0402 | R0402 | R17,R49
1 | NA(10R/R0402) | R0402 | R42
1 | NA(1.0nF/3kV/10%/X7R/SMD/1808 (VISHAY-VJ1808Y102KBHAT4X_ Farnell-2407291)) | C1808 | C20
1 | NA(100nF/16V/10%/X7R/C0402) | C0402 | C29
1 | NA(10uF/6.3V/20%/X5R/C0603) | C0603 | C21
2 | NA(GG0402052R542P) | D0402 | TVS2,TVS3
1 | NA(SMBJ6.0A) | DO214AA | D8
1 | NA(SN74LVC1G04DBVR(SOT23-5)) | SOT-23-5 | U8
2 | NS(HN1x10) | HN1x10 | EXT1,EXT2

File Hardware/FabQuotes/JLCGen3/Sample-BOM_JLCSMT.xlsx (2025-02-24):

Comment | Designator | Footprint | JLCPCB Part #（optional）
100nF | C32,C40,C37,C42,C17,C15,C14,C38,C44 | C_0603_1608Metric | CL10B104KA8NNNC (https://jlcpcb.com/partdetail/1942-CL10B104KA8NNNC/C1590)
6130XX11121_61300611121 | J2,J1 | 61300611121 | C5444523
18pF | C43,C45 | C_0201_0603Metric | C62164
10k | R13,R14 | C_0402_1005Metric | C25531
2.2uF | C9,C39,C36,C34,C12 | C_0603_1608Metric | C1607
22pF | C31,C30 | C_0402_1005Metric | C126502
U.FL-R-SMT-1 | ANT1 | U.FL-R-SMT-1 | C9900006828
1054500101 | J5 | 1054500101 | C134092
5.1K | R21,R26 | R_0402_1005Metric | C25905
LED | D8,D9,D13 | LED_0603_1608Metric | C2286
MountingHole | H1,H2 | MountingHole_2.1mm
0 | R6,R3,R20,R22,R2,R19 | R_0402_1005Metric | C21376
F32R-1A7H1-11024 | J10 | AMPHENOL_F32R-1A7H1-11024 | C3167938
PMEG6010CEJ | D2,D3,D1,D5,D4,D11,D10,D6 | D_SOD-323F | C27636122
4.7k | R7,R9 | R_0402_1005Metric | C25900
0k | R8 | R_0805_2012Metric | C17477
0.1uF | C29,C28 | C_0402_1005Metric | C1525
COIL1 | TP1 | TestPoint_THTPad_2.0x2.0mm_Drill1.0mm
530470210 | J3,J4 | CON_530470210_MOL | C114130
10nF | C41 | C_0402_1005Metric | C1524
499 | R31 | R_0402_1005Metric | C4125
4.7uF | C18 | C_0603_1608Metric | C1705
10k | R10 | R_0805_2012Metric | C17414
COIL2 | TP2 | TestPoint_THTPad_2.0x2.0mm_Drill1.0mm
10k | R18,R16,R17,R12,R11,R5 | R_0402_1005Metric | C25531
BNO055 | U8 | LGA28R50P4X10_380X520X100 | C93216
2nH | L1 | L_0201_0603Metric | C86106
1k | R15,R23,R25 | R_0402_1005Metric | C11702
ABM8G-40.000MHZ-18-D2Y-T | Y2 | CRYSTAL_ABM8G_ABR | C1985459
1.6pF | C35,C33 | C_0402_1005Metric | C88881
ABS07-32.768KHZ-7-T | Y1 | XTAL_ABS07-32.768KHZ-7-T | C276424
6nF | C1 | C_0805_2012Metric | C1752
PTS815 SJM 250 SMTR LFS | SW3,SW1 | SW4_PTS815 SJM 250 SMTR LFS_CNK | C411883
ESP32-S3 | U9 | QFN-56-1EP_7x7mm_P0.4mm_EP3.2x3.2mm | C2913192
1uF | C16,C27,C7,C21,C11,C8,C4,C26,C22,C3 | C_0603_1608Metric | C14664
GD25Q64CSIGR | U2 | SOP8_208MIL_GDV | C395510
NANOSMDC110F-2 | F1 | FUS_NANO_TYCO_TYC | C2649906
10uF | C24,C20,C25,C10,C19,C13 | C_0603_1608Metric | C1691
120R-3A | FB1 | C_0805_2012Metric | C79382
MCP73812T-420I-OT | U3,U1 | SOT-23-5 | C144308
B140-E3 | D7 | D_SMA | C968568
2nH | L2 | L_0402_1005Metric | C2043639
MIC5504-3.3YM5 | U4 | SOT-23-5 | C41348078
2k | R4,R1 | R_0402_1005Metric | C4109
MCP1700x-280xxTT | U6 | SOT-23 | C625349
10uF | C2 | C_0402_1005Metric | C15525
MIC5504-1.8YM5 | U5 | SOT-23-5 | C626116

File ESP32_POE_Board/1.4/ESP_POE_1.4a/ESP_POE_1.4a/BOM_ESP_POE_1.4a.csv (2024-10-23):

Reference | Value | Footprint | Datasheet | Mfr | Mfr P/N | Price | Purchase-URL | Supplier 1 | Supplier 1 P/N | note | Qty
ACT1 | LED/YELLOW/0603 | OLIMEX_LEDs-FP:LED_0603_KA |  | Everlight Elec | 19-21/Y2C-CP1Q2B/4T | 0.0328 | https://www.lcsc.com/product-detail/span-style-background-color-ff0-LED-span-Indication-Discrete_Everlight-Elec-19-21-Y2C-CP1Q2B-4T_C2986008.html | LCSC | C2986008 |  | 1
C2 | 1nF/2000V/10%/X7R/C1206 | OLIMEX_RLC-FP:C_1206_5MIL_DWS_ISO |  | YAGEO | CC1206MKX7RDBB102 | 0.0142 | https://www.lcsc.com/product-detail/Multilayer-Ceramic-Capacitors-MLCC-SMD-SMT_YAGEO-CC1206MKX7RDBB102_C527363.html | LCSC | C527363 |  | 1
C9, C10, C13, C19 | 22uF/6.3V/20%/X5R/C0603 | OLIMEX_RLC-FP:C_0603_5MIL_DWS |  | Samsung Electro-Mechanics | CL10A226MP8NUNE | 0.0123 | https://www.lcsc.com/product-detail/Multilayer-Ceramic-Capacitors-MLCC-SMD-SMT_Samsung-Electro-Mechanics-CL10A226MP8NUNE_C86295.html | LCSC | C86295 |  | 4
C11, C14-C16, C18 | 100nF/16V/10%/X7R/C0402 | OLIMEX_RLC-FP:C_0402_5MIL_DWS |  | YAGEO | CC0402KRX7R7BB104 | 0.0009 | https://www.lcsc.com/product-detail/Multilayer-Ceramic-Capacitors-MLCC-SMD-SMT_YAGEO-CC0402KRX7R7BB104_C60474.html | LCSC | C60474 |  | 5
C12, C24 | 100nF/100V/10%/X7R/C0603 | OLIMEX_RLC-FP:C_0603_5MIL_DWS |  | YAGEO | CC0603KRX7R9BB104 | 0.002 | https://www.lcsc.com/product-detail/Multilayer-Ceramic-Capacitors-MLCC-SMD-SMT_YAGEO-CC0603KRX7R9BB104_C14663.html | LCSC | C14663 |  | 2
C17 | 2.2uF/6.3V/10%/X5R/C0603 | OLIMEX_RLC-FP:C_0603_5MIL_DWS |  | Samwha Capacitor | CS1608X5R225K100NRB | 0.0047 | https://www.lcsc.com/product-detail/Multilayer-Ceramic-Capacitors-MLCC-SMD-SMT_Samwha-span-style-background-color-ff0-Capacitor-span-CS1608X5R225K100NRB_C5189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 | LCSC | C5189830 |  | 1
C20, C23 | 1.0nF/3kV/10%/X7R/SMD/1808(VISHAY-VJ1808Y102KBHAT4X_Farnell-2407291) | OLIMEX_RLC-FP:C_1808(4520)_5MIL_DWS_ISO |  | IHHEC(HOLY STONE ENTERPRISE CO., LTD) | SCC1808X102K502TS | 0.1511 | https://www.lcsc.com/product-detail/Safety-Capacitors_IHHEC-HOLY-STONE-ENTERPRISE-CO-LTD-SCC1808X102K502TS_C2939745.html | LCSC | C2939745 |  | 2
C21 | NA(10uF/6.3V/20%/X5R/C0603) | OLIMEX_RLC-FP:C_0603_5MIL_DWS |  | Samsung Electro-Mechanics | CL10A106MA8NRNC | 0.0166 | https://www.lcsc.com/product-detail/Multilayer-Ceramic-Capacitors-MLCC-SMD-SMT_Samsung-Electro-Mechanics-CL10A106MA8NRNC_C96446.html | LCSC | C96446 |  | 1
C25 | 12pF/50V/5%/COG/C0402 | OLIMEX_RLC-FP:C_0402_5MIL_DWS |  | Samsung Electro-Mechanics | CL05C120JB51PNC | 0.0056 | https://www.lcsc.com/product-detail/Multilayer-Ceramic-Capacitors-MLCC-SMD-SMT_Samsung-Electro-Mechanics-CL05C120JB51PNC_C472446.html | LCSC | C472446 |  | 1
C26 | 470uF/10V/20%/Low_ESR/RM2.5/6.0x11mm | OLIMEX_RLC-FP:CPOL-RM2.5mm_6.3x11mm_PTH |  | CX(Dongguan Chengxing Elec) | GR477M016E12RR0EH4FP0 | 0.0285 | https://www.lcsc.com/product-detail/Aluminum-Electrolytic-Capacitors-Leaded_CX-Dongguan-Chengxing-Elec-GR477M016E12RR0EH4FP0_C3039776.html | LCSC | C3039776 |  | 1
C27 | 15uF/100V/20%/RM2.5/6.3x11mm(Farnell:1281844) | OLIMEX_RLC-FP:CPOL-RM2.5mm_6.3x11mm_PTH |  | Yunxing | EG22GM150F16OTMO | 0.0995 | https://www.lcsc.com/product-detail/Aluminum-Electrolytic-Capacitors-Leaded_Yunxing-EG22GM150F16OTMO_C2841644.html | LCSC | C2841644 |  | 1
D5 | SS510/100V/5A/0.85V/DO214AB(SMC) | OLIMEX_Diodes-FP:DO214AB(SMC)_1(K)-2(A) |  | Yangzhou Yangjie Elec Tech | SS510 | 0.0875 | https://www.lcsc.com/product-detail/Schottky-Diodes_Yangzhou-Yangjie-Elec-Tech-SS510_C5339843.html | LCSC | C5339843 |  | 1
D10 | SMAJ58A/SMA | OLIMEX_Diodes-FP:SMA-KA |  | STMicroelectronics | SMAJ58A-TR | 0.145 | https://www.lcsc.com/product-detail/ESD-and-Surge-Protection-TVS-ESD_STMicroelectronics-SMAJ58A-TR_C132936.html | LCSC | C132936 |  | 1
DCDC1 | F0505S-2WR2(SIP-7) | OLIMEX_Regulators-FP:SIP-7_Universal |  | EVISUN | EVISUN F0505S-3WR2 | 1.7214 | https://www.lcsc.com/product-detail/Isolated-Power-Modules_EVISUN-F0505S-3WR2_C7598643.html | LCSC | C7598643 |  | 1
FET3 | WPM2015-3/TR | OLIMEX_Transistors-FP:SOT23 |  | KUU | WPM2015-3/TR | 0.036 | https://www.lcsc.com/product-detail/MOSFETs_span-style-background-color-ff0-KUU-span-WPM2015-3-TR_C6562215.html | LCSC | C6562215 |  | 1
J3 | HMTSW-102-X-X-S-X | HMTSW-102-X-X-S-X:SAMTEC_HMTSW-102-X-X-S-X |  | MOLEX | 22284020 | 0.0526 | https://www.lcsc.com/product-detail/Pin-Headers_MOLEX-22284020_C234182.html | LCSC | C234182 |  | 1
J4, J6 | C3324132 | CONN_20021111-XX012XXLF_AMP | 20021111-00012T4LF | DEALON | DZ127R-11-09-25 | 0.0343 | https://www.lcsc.com/product-detail/Pin-Headers_DEALON-DZ127R-11-09-25_C2935949.html | LCSC | C3324132 |  | 2
L1 | FB0805/600R/2A | OLIMEX_RLC-FP:L_0805_5MIL_DWS |  | Murata Electronics | BLM21SP601SZ1D | 0.2178 | https://www.lcsc.com/product-detail/span-style-background-color-ff0-Ferrite-span-Beads_Murata-Electronics-BLM21SP601SZ1D_C2661781.html | LCSC | C2661781 | the max current is 1A here | 1
LNK1 | LED/GREEN/0603 | OLIMEX_LEDs-FP:LED_0603_KA |  | Everlight Elec | 18-225/R6G6C-A01/3T | 0.0772 | https://www.lcsc.com/product-detail/LED-Indication-Discrete_Everlight-Elec-18-225-R6G6C-A01-3T_C172883.html | LCSC | C172883 |  | 1
R2, R25, R44 | 10k/R0402 | OLIMEX_RLC-FP:R_0402_5MIL_DWS |  | YAGEO | RC0402FR-0710KL | 0.0005 | https://www.lcsc.com/product-detail/Chip-span-style-background-color-ff0-Resistor-span-Surface-Mount_YAGEO-RC0402FR-0710KL_C60490.html | LCSC | C60490 |  | 3
R3 | 1k/R0402 | OLIMEX_RLC-FP:R_0402_5MIL_DWS |  | YAGEO | RC0402FR-071KL | 0.0006 | https://www.lcsc.com/product-detail/Chip-span-style-background-color-ff0-Resistor-span-Surface-Mount_YAGEO-RC0402FR-071KL_C106235.html | LCSC | C106235 |  | 1
R10-R13 | 49.9R/1%/R0402 | OLIMEX_RLC-FP:R_0402_5MIL_DWS |  | YAGEO | RC0402FR-0749R9P | 0.005 | https://www.lcsc.com/product-detail/Chip-span-style-background-color-ff0-Resistor-span-Surface-Mount_YAGEO-RC0402FR-0749R9P_C851839.html | LCSC | C851839 |  | 4
R14, R15 | 2.2k/R0402 | OLIMEX_RLC-FP:R_0402_5MIL_DWS |  | YAGEO | AC0402JR-072K2L | 0.0008 | https://www.lcsc.com/product-detail/Chip-span-style-background-color-ff0-Resistor-span-Surface-Mount_YAGEO-AC0402JR-072K2L_C144718.html | LCSC | C144718 |  | 2
R22 | 24.9k/1%/R0402 | OLIMEX_RLC-FP:R_0402_5MIL_DWS |  | YAGEO | RT0402BRD0724K9L | 0.0207 | https://www.lcsc.com/product-detail/Chip-span-style-background-color-ff0-Resistor-span-Surface-Mount_YAGEO-RT0402BRD0724K9L_C852664.html | LCSC | C852664 |  | 1
R23 | 180k/1%/R0402 | OLIMEX_RLC-FP:R_0402_5MIL_DWS |  | YAGEO | AC0402FR-07180KL | 0.001 | https://www.lcsc.com/product-detail/Chip-span-style-background-color-ff0-Resistor-span-Surface-Mount_YAGEO-AC0402FR-07180KL_C144794.html | LCSC | C144794 |  | 1
R26 | 12.1k/1%/R0402 | OLIMEX_RLC-FP:R_0402_5MIL_DWS |  | YAGEO | RT0402BRD0712K1L | 0.0204 | https://www.lcsc.com/product-detail/Chip-span-style-background-color-ff0-Resistor-span-Surface-Mount_YAGEO-RT0402BRD0712K1L_C281773.html | LCSC | C281773 |  | 1
R27 | 4.42k/1%/1/16W/R0402 | OLIMEX_RLC-FP:R_0402_5MIL_DWS |  | YAGEO | RT0402BRD074K42L | 0.0172 | https://www.lcsc.com/product-detail/Chip-span-style-background-color-ff0-Resistor-span-Surface-Mount_YAGEO-RT0402BRD074K42L_C513571.html | LCSC | C513571 |  | 1
R28 | 0.03R/1%/R1206 | OLIMEX_RLC-FP:R_1206_5MIL_DWS |  | YAGEO | RL1206FR-070R03L | 0.0121 | https://www.lcsc.com/product-detail/Current-Sense-Resistors-Shunt-Resistors_YAGEO-RL1206FR-070R03L_C375524.html | LCSC | C375524 |  | 1
R33 | 4.7R/R0402 | OLIMEX_RLC-FP:R_0402_5MIL_DWS |  | YAGEO | RC0402FR-074R7L | 0.0013 | https://www.lcsc.com/product-detail/Chip-span-style-background-color-ff0-Resistor-span-Surface-Mount_YAGEO-RC0402FR-074R7L_C137962.html | LCSC | C137962 |  | 1
R34 | 10.5k/1%/R0402 | OLIMEX_RLC-FP:R_0402_5MIL_DWS |  | YAGEO | RC0402FR-0710K5L | 0.0006 | https://www.lcsc.com/product-detail/Chip-span-style-background-color-ff0-Resistor-span-Surface-Mount_YAGEO-RC0402FR-0710K5L_C171695.html | LCSC | C171695 |  | 1
R38 | 56.2k/1%/R0402 | OLIMEX_RLC-FP:R_0402_5MIL_DWS |  | YAGEO | AC0402FR-0756K2L | 0.0011 | https://www.lcsc.com/product-detail/Chip-span-style-background-color-ff0-Resistor-span-Surface-Mount_YAGEO-AC0402FR-0756K2L_C227142.html | LCSC | C227142 |  | 1
R41 | 4.7k/R2512 | OLIMEX_RLC-FP:R_2512_MM_DWS |  | YAGEO | RC2512FK-074K7L | 0.0362 | https://www.lcsc.com/product-detail/Chip-span-style-background-color-ff0-Resistor-span-Surface-Mount_YAGEO-RC2512FK-074K7L_C163339.html | LCSC | C163339 |  | 1
R43 | 130k/R0402 | OLIMEX_RLC-FP:R_0402_5MIL_DWS |  | YAGEO | RT0402BRD07130KL | 0.0195 | https://www.lcsc.com/product-detail/Chip-span-style-background-color-ff0-Resistor-span-Surface-Mount_YAGEO-RT0402BRD07130KL_C852515.html | LCSC | C852515 |  | 1
RM1, RM2 | RA1206_(4X0603)_4B8_2.2k | OLIMEX_RLC-FP:R_MATRIX_4 |  | UNI-ROYAL(Uniroyal Elec) | 4D03WGJ0222T5E | 0.0049 | https://www.lcsc.com/product-detail/Resistor-Networks-Arrays_UNI-ROYAL-Uniroyal-Elec-4D03WGJ0222T5E_C12001.html | LCSC | C12001 |  | 2
T1 | LMUN2211LT1G(SOT-23) | OLIMEX_Transistors-FP:SOT23 |  | LRC | LMUN2211LT1G | 0.0153 | https://www.lcsc.com/product-detail/Digital-Transistors_LRC-LMUN2211LT1G_C12775.html | LCSC | C12775 |  | 1
TVS1 | ESDS314DBVR(SOT-23-5) | OLIMEX_Diodes-FP:SOT-23-5 | https://www.ti.com/lit/gpn/esds314 | Texas Instruments | ESDS314DBVR | 0.2597 | https://www.lcsc.com/product-detail/span-style-background-color-ff0-ESD-span-and-Surge-Protection-TVS-span-style-background-color-ff0-ESD-span_Texas-Instrumen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 | LCSC | C1847859 |  | 1
U2 | TPS2376PW(TSSOP-8) | OLIMEX_IC-FP:TSSOP-8_Pitch-0.65mm_Dimensions-4.40x3.00x1.20mm | https://www.ti.com/lit/gpn/tps2375 | Texas Instruments | TPS2376DDAR-H | 0.6501 | https://www.lcsc.com/product-detail/Power-Over-Ethernet-PoE-Controllers_Texas-Instruments-TPS2376DDAR-H_C544899.html | LCSC | C544899 | we use the thermal pad version | 1
U4 | LAN8710A-EZC(QFN32) | OLIMEX_IC-FP:QFN32_EP(33)_5.00x5.00x0.90mm_Pitch_0.50mm |  | Microchip Tech | LAN8710A-EZC-TR | 0.8993 | https://www.lcsc.com/product-detail/Ethernet-Transceivers_Microchip-Tech-LAN8710A-EZC-TR_C46185.html | LCSC | C46185 |  | 1
U5 | TX4138(ESOIC-8) | OLIMEX_Regulators-FP:ESOIC-8 | https://datasheet.lcsc.com/lcsc/1811141153_XDS-TX4138_C329267.pdf | XDS | TX4138 | 0.7668 | https://www.lcsc.com/product-detail/DC-DC-Converters_XDS-TX4138_C329267.html | LCSC | C329267 |  | 1

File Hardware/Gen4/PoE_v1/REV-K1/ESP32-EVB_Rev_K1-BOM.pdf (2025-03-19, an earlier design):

ESP32-EVB_Rev_K1-BOM | 18/04/2023
Quantity | Designation | Package | Designator
1 | 0R(board_mounted) | R0603 | R25
1 | 6.8R/R1206 | R1206 | R53
2 | 10R/R0603 | R0603 | R36,R43
5 | 49.9R/1%/R0402 | R0402 | R28,R31,R32,R33,R58
1 | 120R/R1206 | R1206 | R47
5 | 220R/R0603 | R0603 | R14,R16,R26,R27,R37
1 | 330R/R0603 | R0603 | R13
1 | 680R/R0603 | R0603 | R15
6 | 1k/R0603 | R0603 | R1,R5,R41,R42,R50,R55
1 | 2k/1%/R0603 | R0603 | R8
6 | 2.2k/R0603 | R0603 | R3,R4,R7,R11,R18,R21
3 | RA1206_(4X0603)_4B8_2.2k | RA1206 | RM1,RM2,RM3
15 | 10k/R0603 | R0603 | R2,R6,R22,R23,R24,R29, R30,R34,R35,R38,R40, R45,R49,R51,R56
1 | 12.1k/1%/R0603 | R0603 | R39
1 | 49.9k/1%/R0603 | R0603 | R20
1 | 220k/R0603 | R0603 | R19
1 | 100k/R0603 | R0603 | R52
2 | 470k/R0603 | R0603 | R9,R10
3 | FB0805/600R/2A | L0805 | L1,L3,L4
1 | 2.2uH/1.5A/DCR=72mR/ 20%/3.00x3.00x1.50mm/ CD32(NR3015T2R2M) | CD32 | L2
2 | 27pF/50V/5%/C0G/C0603 | C0603 | C21,C22
1 | 1nF/50V/5%/NPO(COG)/C0603 | C0603 | C18
9 | 100nF/50V/20%/Y5V/C0603 | C0603 | C11,C13,C14,C15,C17, C24,C25,C27,C30
1 | 1nF/2000V/10%/X7R/C1206 | C1206 | C19
2 | 1uF/10V/10%/X5R/C0603 | C0603 | C31,C32
1 | 2.2uF/6.3V/10%/X5R/C0603 | C0603 | C16
1 | 10uF/6.3V/20%/X5R/C0603 | C0603 | C26
8 | 22uF/6.3V/20%/X5R/C0603 | C0603 | C5,C6,C7,C8,C9,C12,C23,C29
3 | 47uF/6.3V/20%/X5R/C0805 | C0805 | C2,C4,C10
1 | LED/Yellow/0603 | LED0603 | CHARGE1
1 | LED/RED/0603 | LED0603 | PWRLED1
2 | LED/GREEN/0603 | LED0603 | LED1,LED2
1 | LED/IR333-A/5mm | LED-5mm-PTH | LED3
1 | BAT54A(SOT23-3) | SOT23-3 | D10
2 | BAT54C(SOT23-3) | SOT23-3 | U9,U10
6 | 1N5819S4(SOD-123) | SOD-123 | D1,D3,D5,D7,D8,D9
2 | 1N5822/SS34/SMA | SMA | D4,D6
1 | ESDS314DBVR(SOT-23-5) | SOT-23-5 | TVS1
1 | SMBJ6.0A(DO-214AA) | DO214AA | D2
5 | BC817-40(SOT23) | SOT23 | Q1,Q2,Q4,Q5,Q7
1 | BSS138 | SOT23 | FET4
3 | WPM2015-3/TR | SOT23 | FET1,FET2,FET3
1 | BL4054B-42TPRN(SOT23-5) | SOT-23-5 | U1
1 | CH340T(SSOP20W) | SSOP-20W | U5
1 | ESP-WROOM-32 | ESP-WROOM-32 | U3
1 | LAN8710A-EZC(QFN32) | QFN32 | U4

ESP32-EVB_Rev_K1-BOM | 18/04/2023
1 | VS1838B | RPM7236-H8 | U7
1 | SIT1050T(SOIC-8_150mil) | SOIC-8 | U6
1 | SY8089AAAC(SOT23-5) | SOT-23-5 | U2
1 | HX7027(SOT-23) | SOT-23 | U11
1 | Q12MHz/20pF/30ppm/ 2P/HC-49SM(SMD) | Q_49U3HMS | Q3
1 | Q50MHz/25ppm/3V/4P/5x3.2mm | 5032-4P_HCX-3S | CR1
2 | RAS-0515 | Relay_RAS-05-15 | REL1,REL2
2 | T1107A(6x3,8x2,5MM) | T1107A(6x3,8x2,5MM) | BUT1,RST1
1 | BH10S | ML10 | UEXT1
1 | DW02R | DW02R | BAT1
1 | MISB-SWMM-5B-LF(USB_MICRO) | MISB-SWMM-5B_LF | USB-UART1
1 | PWRJ-2mm(YDJ-1134) | PWRJ-2mm | PWR1
1 | RJLD-060TC1(LPJ4013EDNL) | RJLBC-060TC1 | LAN1
1 | TB3-3.5mm | TB3-3.5mm | CAN1
2 | TB3-DG306-5.0-3P | DG306-5.0_3P | CON1,CON2
1 | TFC-WXCP11-08-LF | TFC-WXCP11-08-LF | MICRO_SD1
2 | Opened | SJ | CAN_T1,PHY_RST1
1 | Closed(1-2)/Opened(2-3) | SJ_2 | 5.0V/3.3V1
1 | Opened(2-3)/Soldered(1-2) | SJ_2 | BAT/BUT1
6 | NA/R0603 | R0603 | R12,R17,R44,R46,R48,R54
1 | NA(1k/R0603) | R0603 | R57
1 | NA(FB0805/600R/2A) | L0805 | L5
1 | NA(1nF/2000V/10%/X7R/C1206) | C1206 | C20
1 | NA(470nF/16V/10%/X7R/C0603) | C0603 | C28
2 | NA(47uF/6.3V/20%/X5R/C0805) | C0805 | C1,C3
1 | NA(NCP303LSN27T1G(SOT-23-5)) | SOT-23-5 | U8
1 | NA(HN2x20) | HN2x20 | EXT1
1 | NA(TB2 DG306-5.0-2P) | DG306-5.0_2P | PWR2

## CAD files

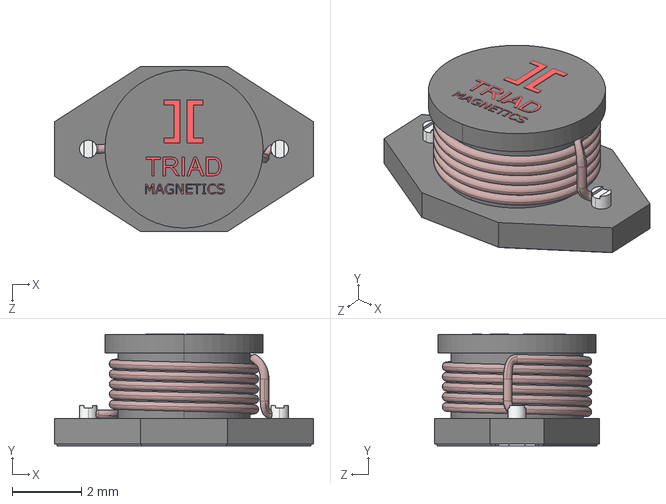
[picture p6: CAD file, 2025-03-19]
Hardware/Example_Schematics/ESP32_POE/ESP32-PoE-ISO/ESP32-PoE-ISO-Rev.K/3d/L_AX97-103R3.step
7.49 x 3.24 x 4.78 mm

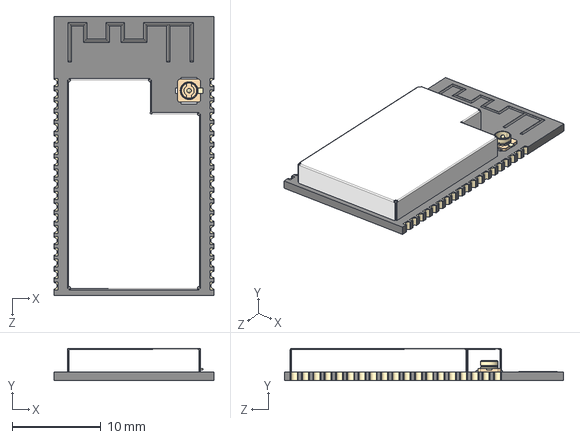
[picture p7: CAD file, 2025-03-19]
Hardware/Example_Schematics/ESP32_POE/ESP32-PoE-ISO/ESP32-PoE-ISO-Rev.L/3d/ESP32-WROVER-I-56544.STEP
18.0 x 3.65 x 31.4 mm

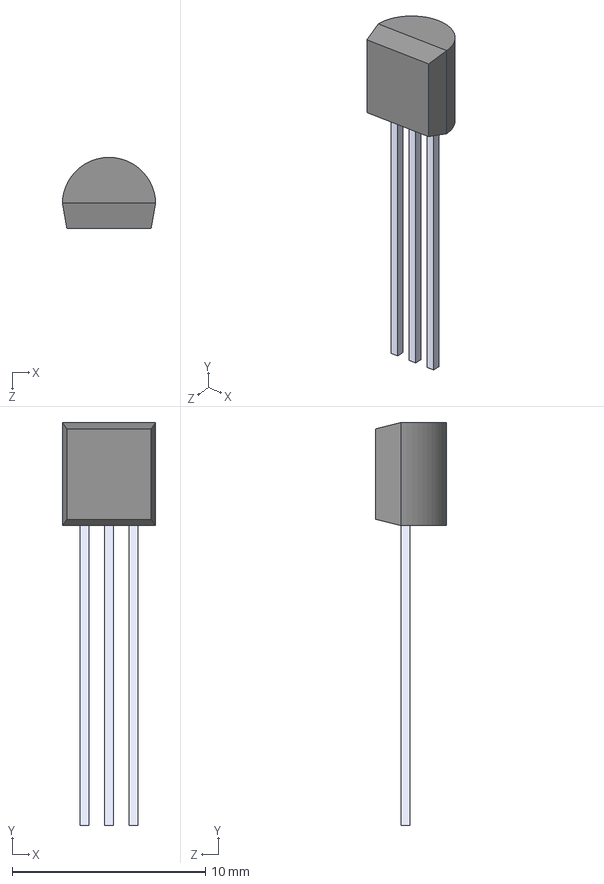
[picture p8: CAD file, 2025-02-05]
Hardware/Gen2Dev/InnerBoard/2.1/InnerBoard_rev2.1/FootprintsRevised/MCP100-270DI_TO/MCP100-270DI_TO.step
4.83 x 20.8 x 3.68 mm

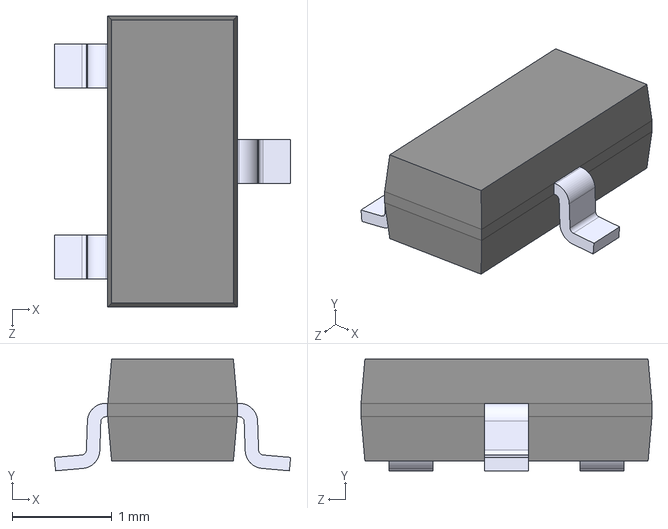
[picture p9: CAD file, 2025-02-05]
Hardware/Gen2Dev/InnerBoard/2.1/InnerBoard_rev2.1/FootprintsRevised/MCP100T-270I_TT/MCP100T-270I_TT.step
2.37 x 1.12 x 2.92 mm

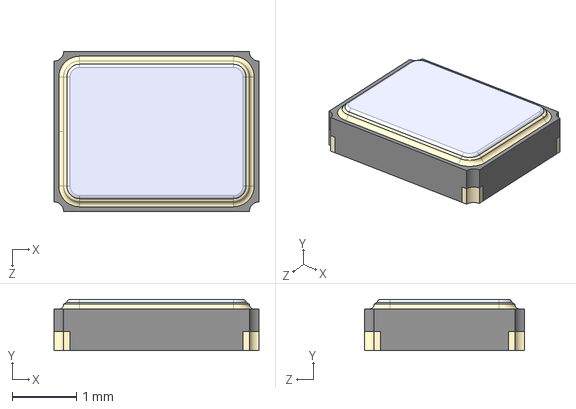
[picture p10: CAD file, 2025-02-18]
Hardware/Gen2Dev/InnerBoard/2.2/footprints/ECS_120_20_33_CKM_TR3/ECS-120-20-33-CKM-TR3.step
3.20 x 0.8 x 2.50 mm

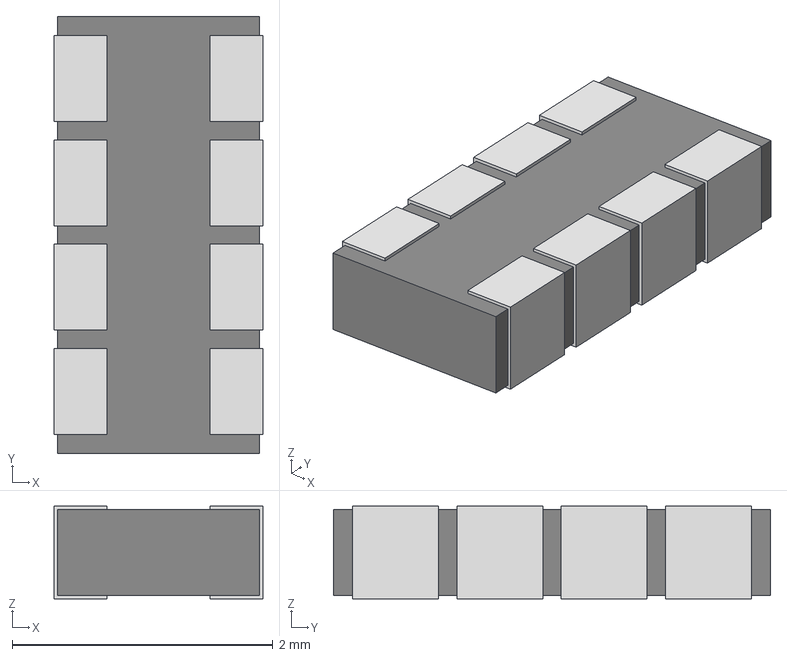
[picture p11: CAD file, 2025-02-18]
Hardware/Gen2Dev/InnerBoard/2.2/footprints/TC164_JR_072K2L/YAG_TC164_YAG.step
1.60 x 3.35 x 0.712 mm

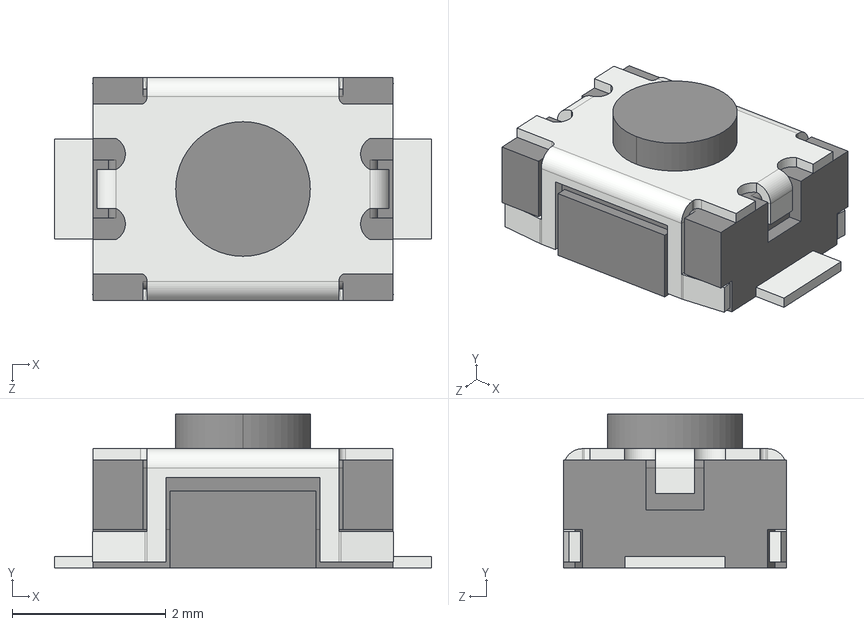
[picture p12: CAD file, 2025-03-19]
Hardware/Example_Schematics/ESP32_POE/ESP32-PoE-ISO/ESP32-PoE-ISO-Rev.K/3d/it1185.step
4.90 x 2.00 x 2.90 mm

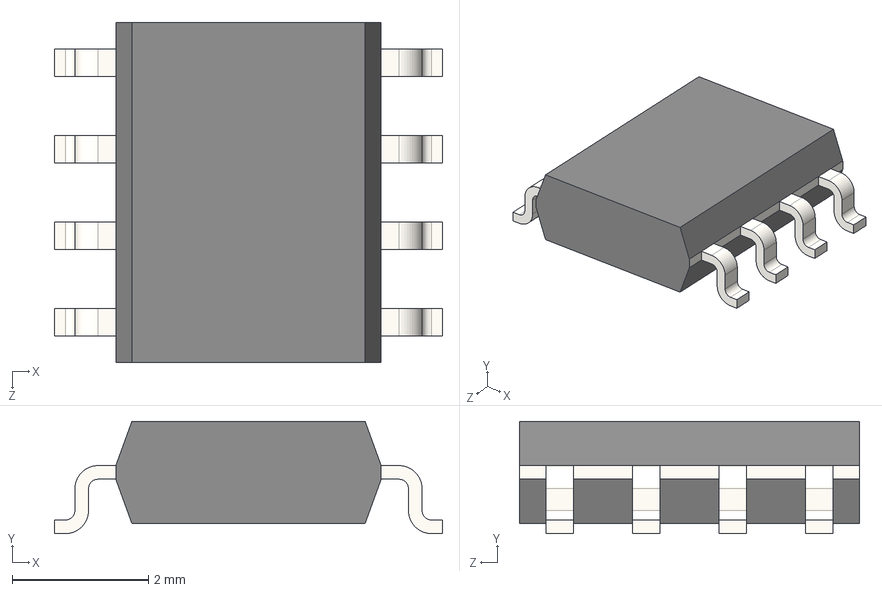
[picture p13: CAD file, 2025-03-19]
Hardware/Example_Schematics/ESP32_POE/ESP32-PoE-ISO/ESP32-PoE-ISO-Rev.L/3d/SL08.step
5.70 x 1.65 x 5.00 mm

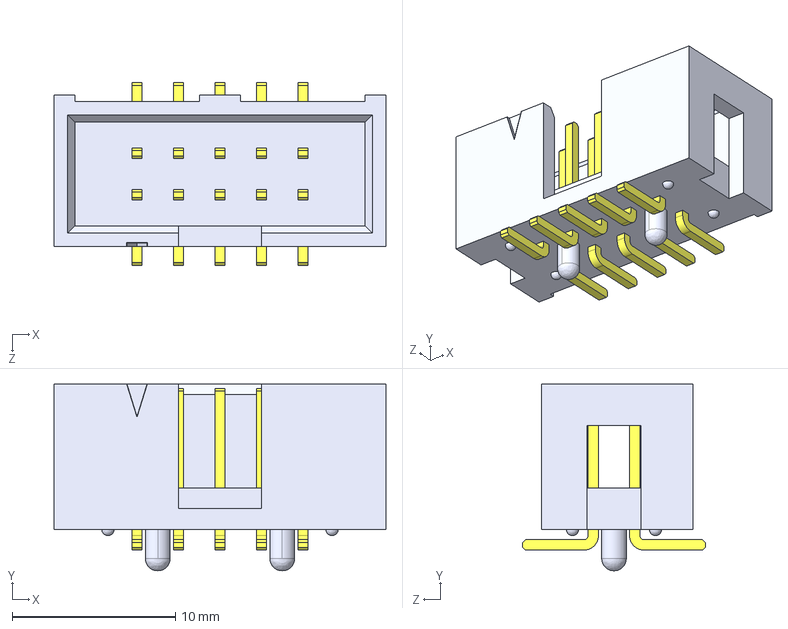
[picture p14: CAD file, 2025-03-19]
Hardware/Example_Schematics/ESP32_POE/ESP32-PoE-ISO/ESP32-PoE-ISO-Rev.L/3d/UEXT-SMD.STEP
20.3 x 11.4 x 11.2 mm
User Library-HTST-105-01-F-DV-A__HTST-105-01-DV-A_header
User Library-HTST-105-01-F-DV-A__HTST-First_Position_Indicator
User Library-HTST-105-01-F-DV-A__T-1S6-05-01-DV_

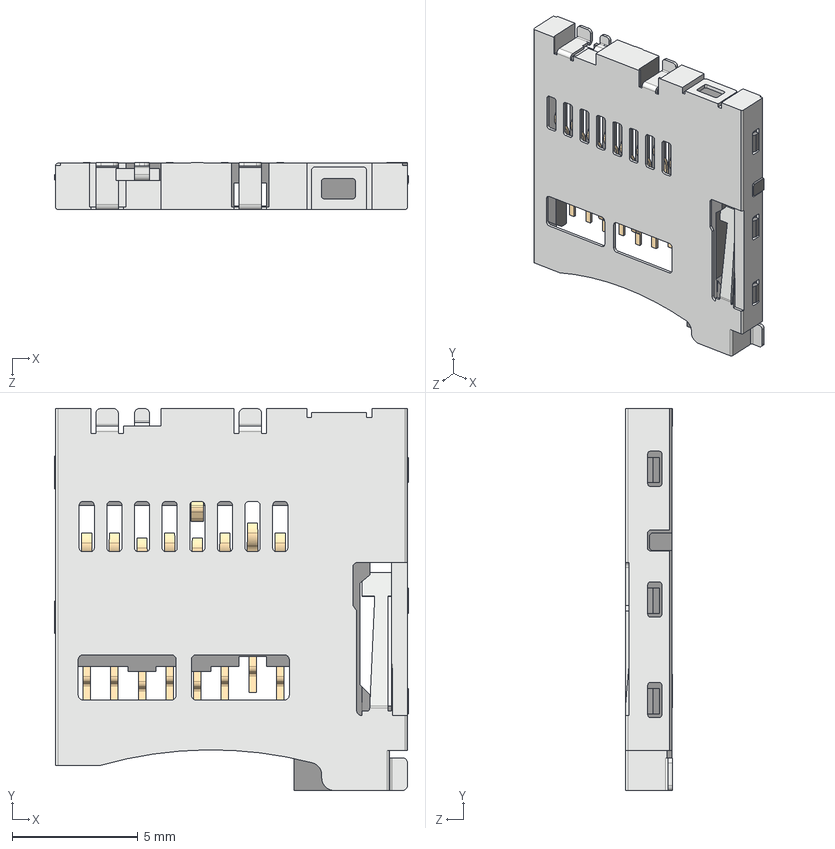
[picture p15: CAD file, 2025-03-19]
Hardware/Example_Schematics/ESP32_POE/ESP32-PoE-ISO/ESP32-PoE-ISO-Rev.K/3d/microSD.step
14.1 x 15.2 x 1.88 mm

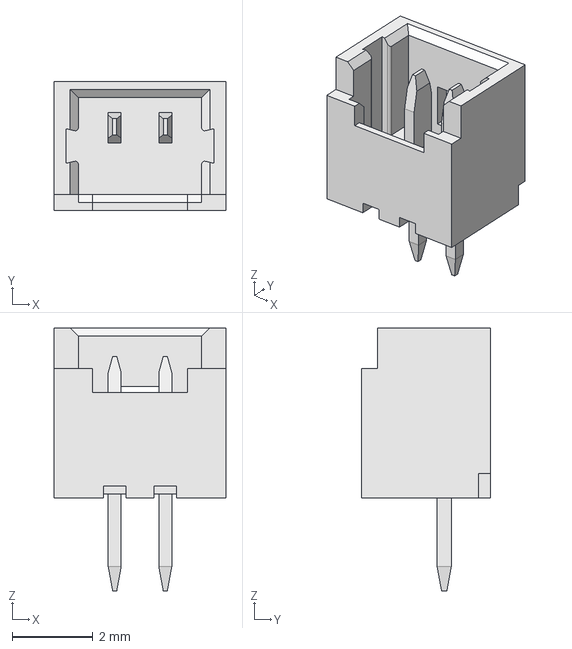
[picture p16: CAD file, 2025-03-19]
Hardware/Example_Schematics/ESP32_POE/ESP32-PoE-ISO/ESP32-PoE-ISO-Rev.L/3d/Molex_PicoBlade_530470210.step
4.25 x 3.20 x 6.50 mm

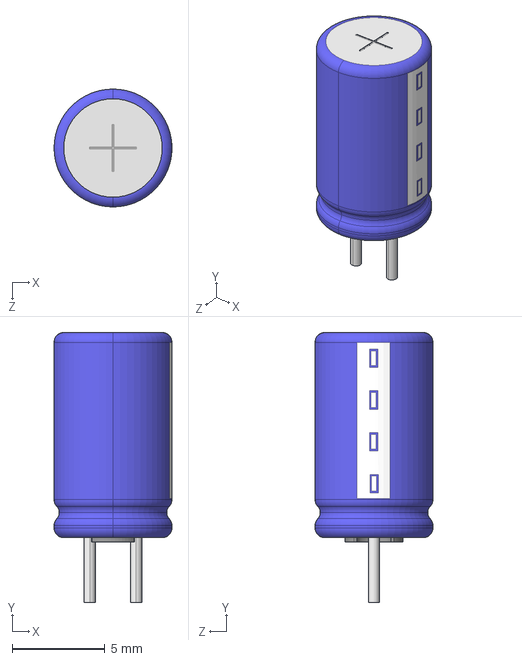
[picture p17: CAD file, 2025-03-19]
Hardware/Example_Schematics/ESP32_POE/ESP32-PoE-ISO/ESP32-PoE-ISO-Rev.K/3d/Cap_PTH_6_3x11x2_5mm.step
6.35 x 14.5 x 6.35 mm

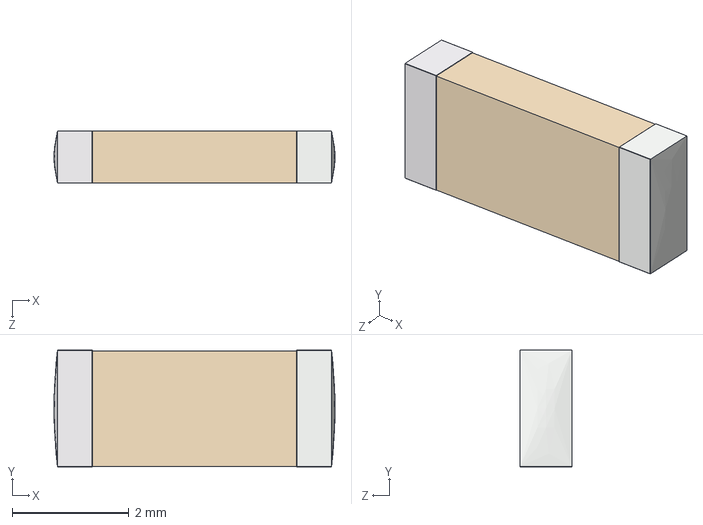
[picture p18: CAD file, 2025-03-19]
Hardware/Example_Schematics/ESP32_POE/ESP32-PoE-ISO/ESP32-PoE-ISO-Rev.L/3d/SMD_Ceramic_Capacitors_1808(4520).step
4.82 x 2.00 x 0.9 mm

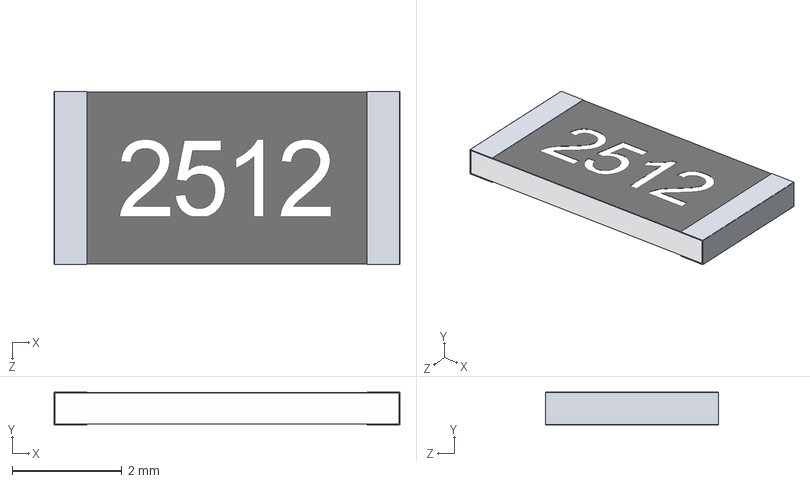
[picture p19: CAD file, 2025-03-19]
Hardware/Example_Schematics/ESP32_POE/ESP32-PoE-ISO/ESP32-PoE-ISO-Rev.K/3d/R_SMD 2512.STEP
6.30 x 0.6 x 3.15 mm
2512 BODY
2512 PAD x 2
2512 OPIS

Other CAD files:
Hardware/Example_Schematics/ESP32_POE/ESP32-PoE-ISO/ESP32-PoE-ISO-Rev.K/3d/DO-214AB_SMC.step
Hardware/Example_Schematics/ESP32_POE/ESP32-PoE-ISO/ESP32-PoE-ISO-Rev.K/3d/Connector_1Port_RJ45_Magjack_10-100Base-T_AutoMDIX_PoE_Wurth_Electronics-7499211002A_DigiKey-732-4976-ND.step
Hardware/Example_Schematics/ESP32_POE/ESP32-PoE-ISO/ESP32-PoE-ISO-Rev.K/3d/Micro_SD_card.step
Hardware/Example_Schematics/ESP32_POE/ESP32-PoE-ISO/ESP32-PoE-ISO-Rev.K/3d/SIP-7.step
Hardware/Example_Schematics/ESP32_POE/ESP32-PoE-ISO/ESP32-PoE-ISO-Rev.K/3d/TSSOP-8_P0.65mm.STEP
Hardware/Example_Schematics/ESP32_POE/ESP32-PoE-ISO/ESP32-PoE-ISO-Rev.L/3d/Connector_1Port_RJ45_Magjack_10-100Base-T_AutoMDIX_PoE_Wurth_Electronics-7499211002A_DigiKey-732-4976-ND.step
Hardware/Example_Schematics/ESP32_POE/ESP32-PoE-ISO/ESP32-PoE-ISO-Rev.L/3d/DO-214AB_SMC.step
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

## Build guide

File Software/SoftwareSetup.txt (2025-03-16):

How to setup Arduino (for external sensing board):
- Download from Arduino website
- Follow instructions from https://wiki.seeedstudio.com/xiao_esp32s3_getting_started/#software-preparation
- Open the CameraWebServer.ino (software for external sensing board, includes WIFI CAM IMU LED)
- May have to manually add file in Arduino for imu_function.h and imu_function.cpp (I created these because the BNO055 library conflicts with the esp_camera library in sensor_t definition, so they must be isolated in different cpp files with no definition exposed in the h file)
-Go to Library Manager, search for "BNO055", and install the "Adafruit BNO055" library
- Compile and flash using XIAO ESP32S3 devices and whichever COM it uses
- Open the serial monitor to check IMU data or the http://192.168.137.* that the camera stream will be hosted on
- Maybe need to press the RST button on the ESP board

How to setup ESP-IDF v4.4 (for internal POE board):
- Some things to note about the POE board:
	- Uses LAN8710A ethernet chip (compatible with LAN8720 code)
	- This chip uses RMII (Reduced media independent interface) rather than SPI like other ethernet chips
	- Does not seem like the POE board has Auto-MDIX, so a crossover cable must be used

- Since the eth2ap example code provided by Olimex is incompatible with new versions of ESP-IDF due to differing libraries and refactoring, we must install v4.4 of ESP-IDF. However, Espressif only supports the newest versions v5.*. Therefore, the installer will not work, and we must source the v4.4 framework from the Github repo.
- https://espressif-docs.readthedocs-hosted.com/projects/esp-idf/en/stable/get-started/windows-setup-scratch.html
- git clone the ESP-IDF v4.4.8 (git clone -b v4.4.8 --recursive https://github.com/espressif/esp-idf.git esp-idf-v4.4.8
cd esp-idf-v4.4.8/)
- Install latest Cmake stable release
- Install latest ninja stable release
- Add ninja.exe to env variable "Path" (C:\Program Files\ninja.exe if under Program Files)
- Install Python (some dependencies are incompatible with the latest version of Python, so you may have to downgrade to Python 3.12 or lower)
- Run "pip install --user pyserial"
- Download precompiled toolchain (https://dl.espressif.com/dl/xtensa-esp32-elf-gcc8_2_0-esp-2020r2-win32.zip) and unzip to any location
- Add the file location of the bin folder in toolchain to system environment variables under "Path" (I unzipped the toolchain in Program Files, so add C:\Program Files\xtensa-esp32-elf\bin under "Path"
- May also need to add new env variables IDF_PATH and IDF_TOOLS_PATH with value C:\Espressif\frameworks\esp-idf-v4.4.8 or wherever you git cloned the ESP-IDF repo
- Then add %IDF_PATH%\tools under "Path"
- Open command prompt and go to directory of esp-idf-v4.4.8
- Run install.bat
- Run export.bat (this must be run every time command prompt is opened to set environment)
- Go to ESP32-PoE_Eth_to_AP_v4.4 in command prompt
- Run idf.py set-target esp32
- To config settings, run "idf.py menuconfig"
- in Ethernet, change the following settings
WITH INTERNAL OSCILLATOR (Olimex POE):
CONFIG_ETH_ENABLED=y
CONFIG_ETH_USE_ESP32_EMAC=y
CONFIG_ETH_PHY_INTERFACE_RMII=y
# CONFIG_ETH_RMII_CLK_INPUT is not set
CONFIG_ETH_RMII_CLK_OUTPUT=y
# CONFIG_ETH_RMII_CLK_OUTPUT_GPIO0 is not set
CONFIG_ETH_RMII_CLK_OUT_GPIO=17
CONFIG_ETH_DMA_BUFFER_SIZE=1536
CONFIG_ETH_DMA_RX_BUFFER_NUM=10
CONFIG_ETH_DMA_TX_BUFFER_NUM=10
# CONFIG_ETH_USE_SPI_ETHERNET is not set
# CONFIG_ETH_USE_OPENETH is not set
- In EXAMPLE CONFIGURATION, change the following settings
CONFIG_EXAMPLE_GPIO_RANGE_MIN=0
CONFIG_EXAMPLE_GPIO_RANGE_MAX=33
CONFIG_EXAMPLE_USE_INTERNAL_ETHERNET=y
# CONFIG_EXAMPLE_USE_DM9051 is not set
# CONFIG_EXAMPLE_USE_W5500 is not set
# CONFIG_EXAMPLE_USE_KSZ8851SNL is not set
# CONFIG_EXAMPLE_ETH_PHY_IP101 is not set
# CONFIG_EXAMPLE_ETH_PHY_RTL8201 is not set
CONFIG_EXAMPLE_ETH_PHY_LAN87XX=y
# CONFIG_EXAMPLE_ETH_PHY_DP83848 is not set
# CONFIG_EXAMPLE_ETH_PHY_KSZ8041 is not set
# CONFIG_EXAMPLE_ETH_PHY_KSZ8081 is not set
CONFIG_EXAMPLE_ETH_MDC_GPIO=23
CONFIG_EXAMPLE_ETH_MDIO_GPIO=18
CONFIG_EXAMPLE_ETH_PHY_RST_GPIO=-1
CONFIG_EXAMPLE_ETH_PHY_ADDR=0
CONFIG_EXAMPLE_WIFI_SSID="Vcc-AP"
CONFIG_EXAMPLE_WIFI_PASSWORD="12345678"
CONFIG_EXAMPLE_WIFI_CHANNEL=1
CONFIG_EXAMPLE_MAX_STA_CONN=4
- May need to turn on CONFIG_FREERTOS_ENABLE_BACKWARD_COMPATIBILITY

WITH EXTERNAL OSCILLATOR (Olimex EVB):
- Serial flasher config -> Flash Size (8 MB) // Maybe should be 4 MB for EVB
- Example Configuration -> Ethernet Type (Internal EMAC)
			-> Ethernet PHY Device (LAN87xx)
			-> (23) SMI MDC GPIO number
			-> (18) SMI MDIO GPIO number
			-> (-1) PHY Reset GPIO number
			-> (0) PHY Address
			-> (Vcc-AP) Wi-Fi SSID
			-> (12345678) Wi-Fi Password
			-> (1) WiFi channel
			-> (4) Maximum STA connections
- Component config 	-> ESP32-specific -> CPU frequency (240 MHz)
			-> Ethernet -> Support ESP32 internal EMAC controller	-> PHY interface (Reduced Media Independent Interface (RMII))
										-> RMII clock mode (Input RMII clock from external)
										-> (1536) Ethernet DMA buffer size (Byte)
										-> (10) Amount of Ethernet DMA Rx buffers
										-> (10) Amount of Ethernet DMA Tx buffers
			-> HTTP Server -> [*] WebSocket server support
			-> FreeRTOS -> (1000) Tick rate (Hz)

- However I have already changed and pushed these values in the sdkconfig file, so no changes should be necessary if you pulled the sdkconfig file, where the menuconfigs are saved
- Connect the ESP-POE
- Run "idf.py -p COM* build flash monitor" to build, flash, and open the serial monitor, with COM* replaced with whichever COM the ESP-POE is connected to, like COM7
- These commands can be run separately like "idf.py -p COM* monitor" to open the serial monitor when no changes have been made
- Go to Control Panel->Network and Internet->Network Connections on your PC
- Right-click Wi-Fi, and Properties->Sharing. Check "Allow other network users to connect through this computer's Internet connection" and choose Ethernet. The ethernet static IP should be changed to 192.168.137.*. You can check under Properties->IPv4. To access anything on the ESP32 LAN, its static IP must be in the same subnet 192.168.137.* and subnet mask 255.255.255.0
- Reset the ESP-POE board
- Then the ESP-POE should initialize the softAP for WiFi, then initialize Ethernet. Now you can connect the external sensing board or any other device using the SSID and password set in the config (I set SSID="Vcc-AP" and pass="12345678")
- When connecting devices, it should show a message in the serial monitor with new STA IP
- Otherwise, reset the external ESP

Currently, the camera stream runs very slowly through the ethernet interface.
Some things to try:
- Different combinations of DMA buffer sizes and DMA Rx and Tx buffer nums
- Firewall issue?
- change values of FLOW_CONTROL_QUEUE_TIMEOUT_MS, FLOW_CONTROL_QUEUE_LENGTH, or FLOW_CONTROL_WIFI_SEND_TIMEOUT_MS (suggested by https://github.com/OLIMEX/ESP32-POE/tree/master/SOFTWARE/ESP-IDF/ESP32-PoE_Eth_to_AP_v4.4)

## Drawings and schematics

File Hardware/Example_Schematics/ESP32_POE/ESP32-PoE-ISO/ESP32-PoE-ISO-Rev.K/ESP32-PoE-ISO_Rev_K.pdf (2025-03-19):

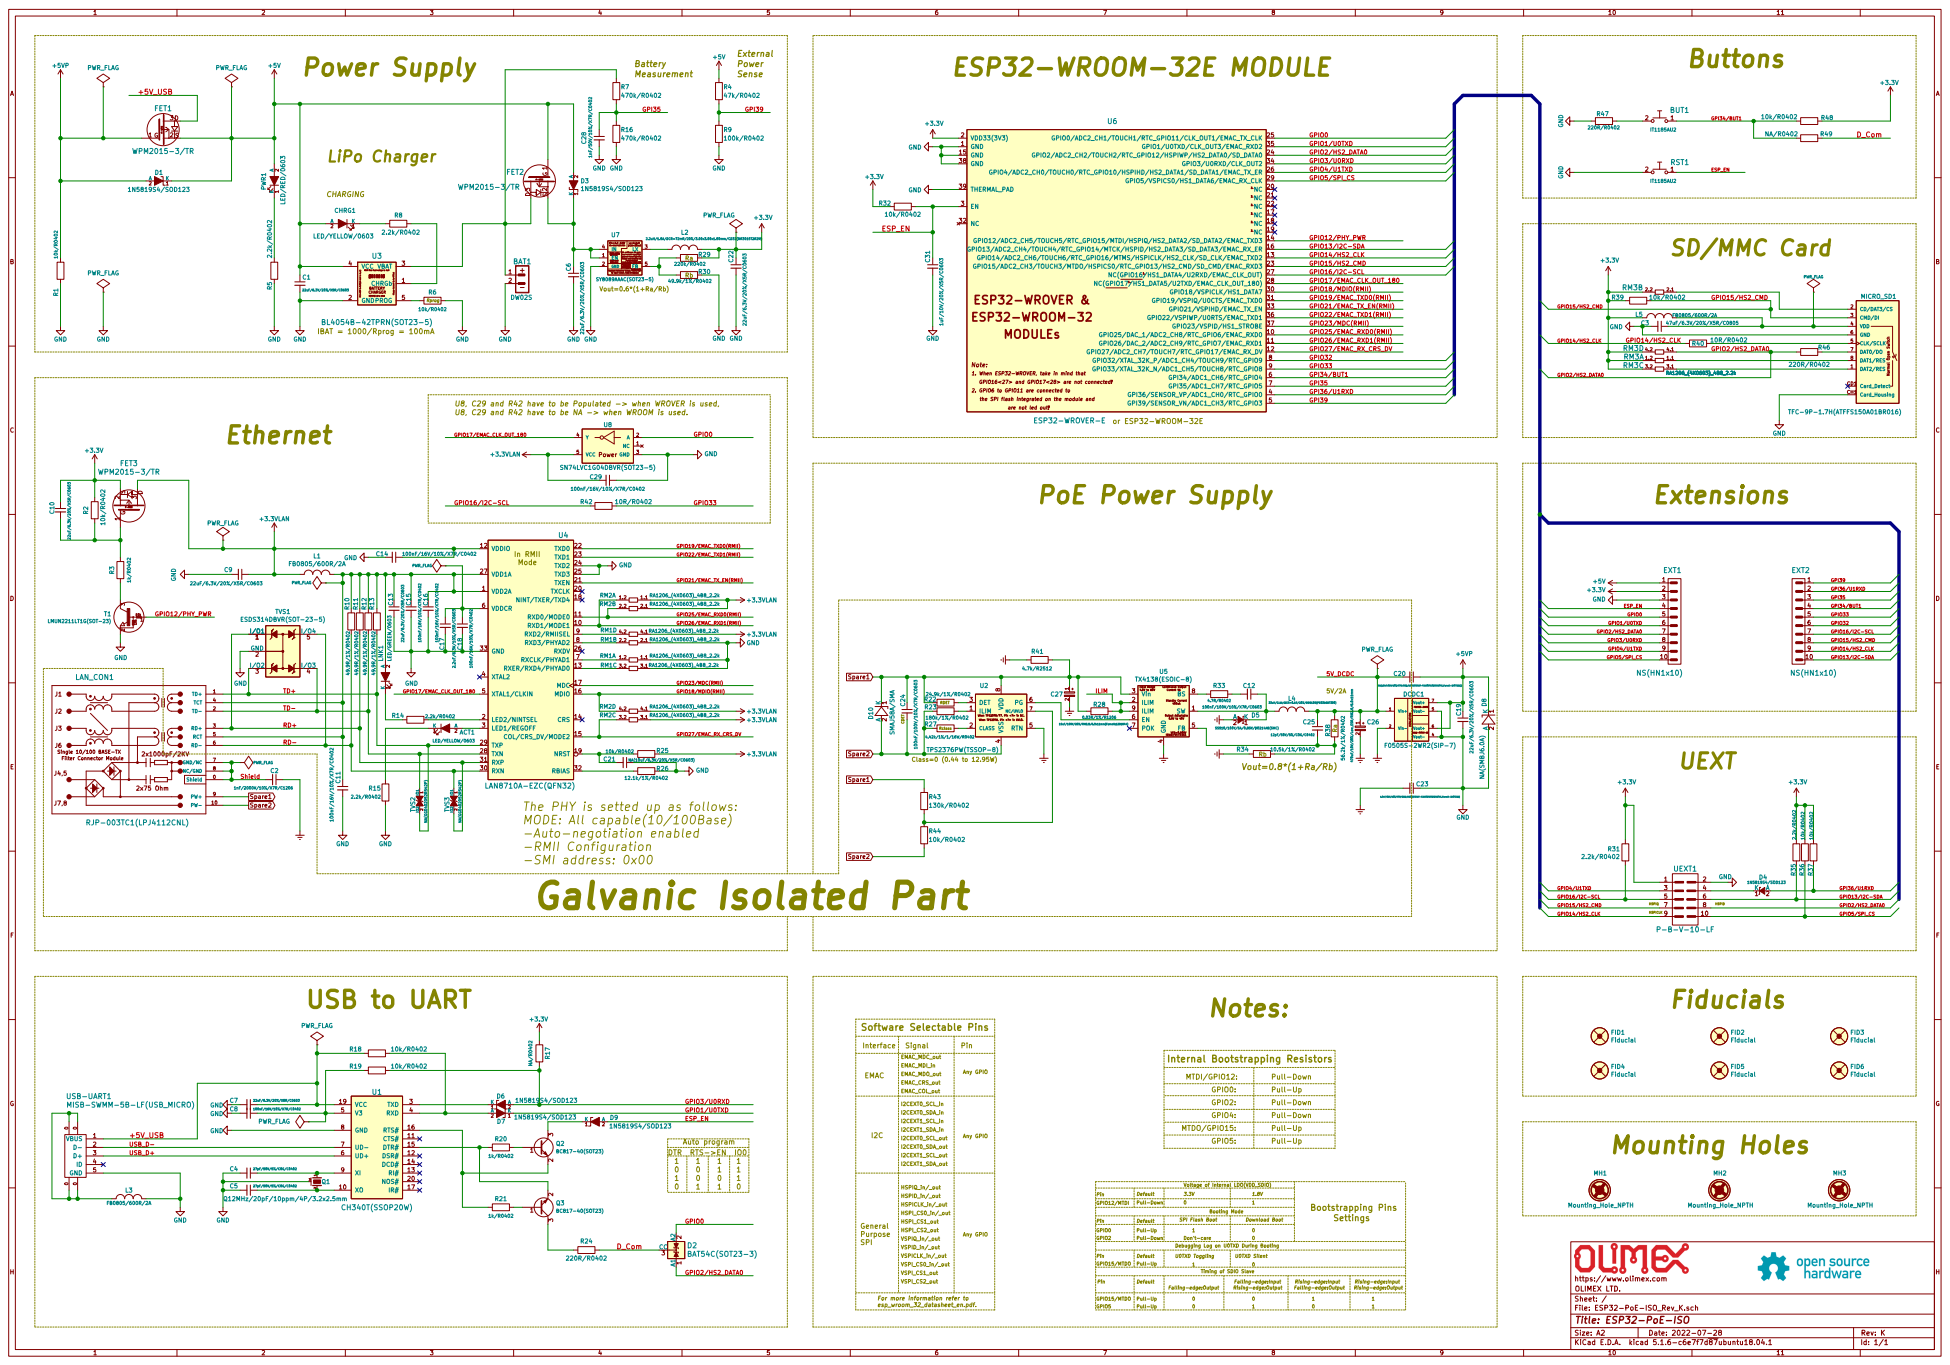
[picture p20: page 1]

2. 2. 2. 2. 2. 2. 2. GPIO6 to GPIO11 are connected to are not led out! ESP32-WROOM-32 ESP32-WROVER &

load current capability! Lx=2.2uH

Do not float. Enable control. FB Input Current, I(FB)=50nA(max) Feedback Reference Voltage, V(REF)=0.6V

1. 1. 1. When ESP32-WROVER, take in mind that

GPIO16<27> and GPIO17<28> are not connected! MODULEs

4 FB 5 EN 6 POK 7 BS 8

Interface The PHY is setted up as follows:
MODE: All capable(10/100Base)
-Auto-negotiation enabled
-RMII Configuration
-SMI address: 0x00

Signal Software Selectable Pins

Auto program
SPI Flash Boot Pull-Up Pull-Down DTR RTS->EN IO0

Falling-edge:Output Pull-Down For more information refer to esp_wroom_32_datasheet_en.pdf.

Id: 1/1 Title: ESP32-PoE-ISO

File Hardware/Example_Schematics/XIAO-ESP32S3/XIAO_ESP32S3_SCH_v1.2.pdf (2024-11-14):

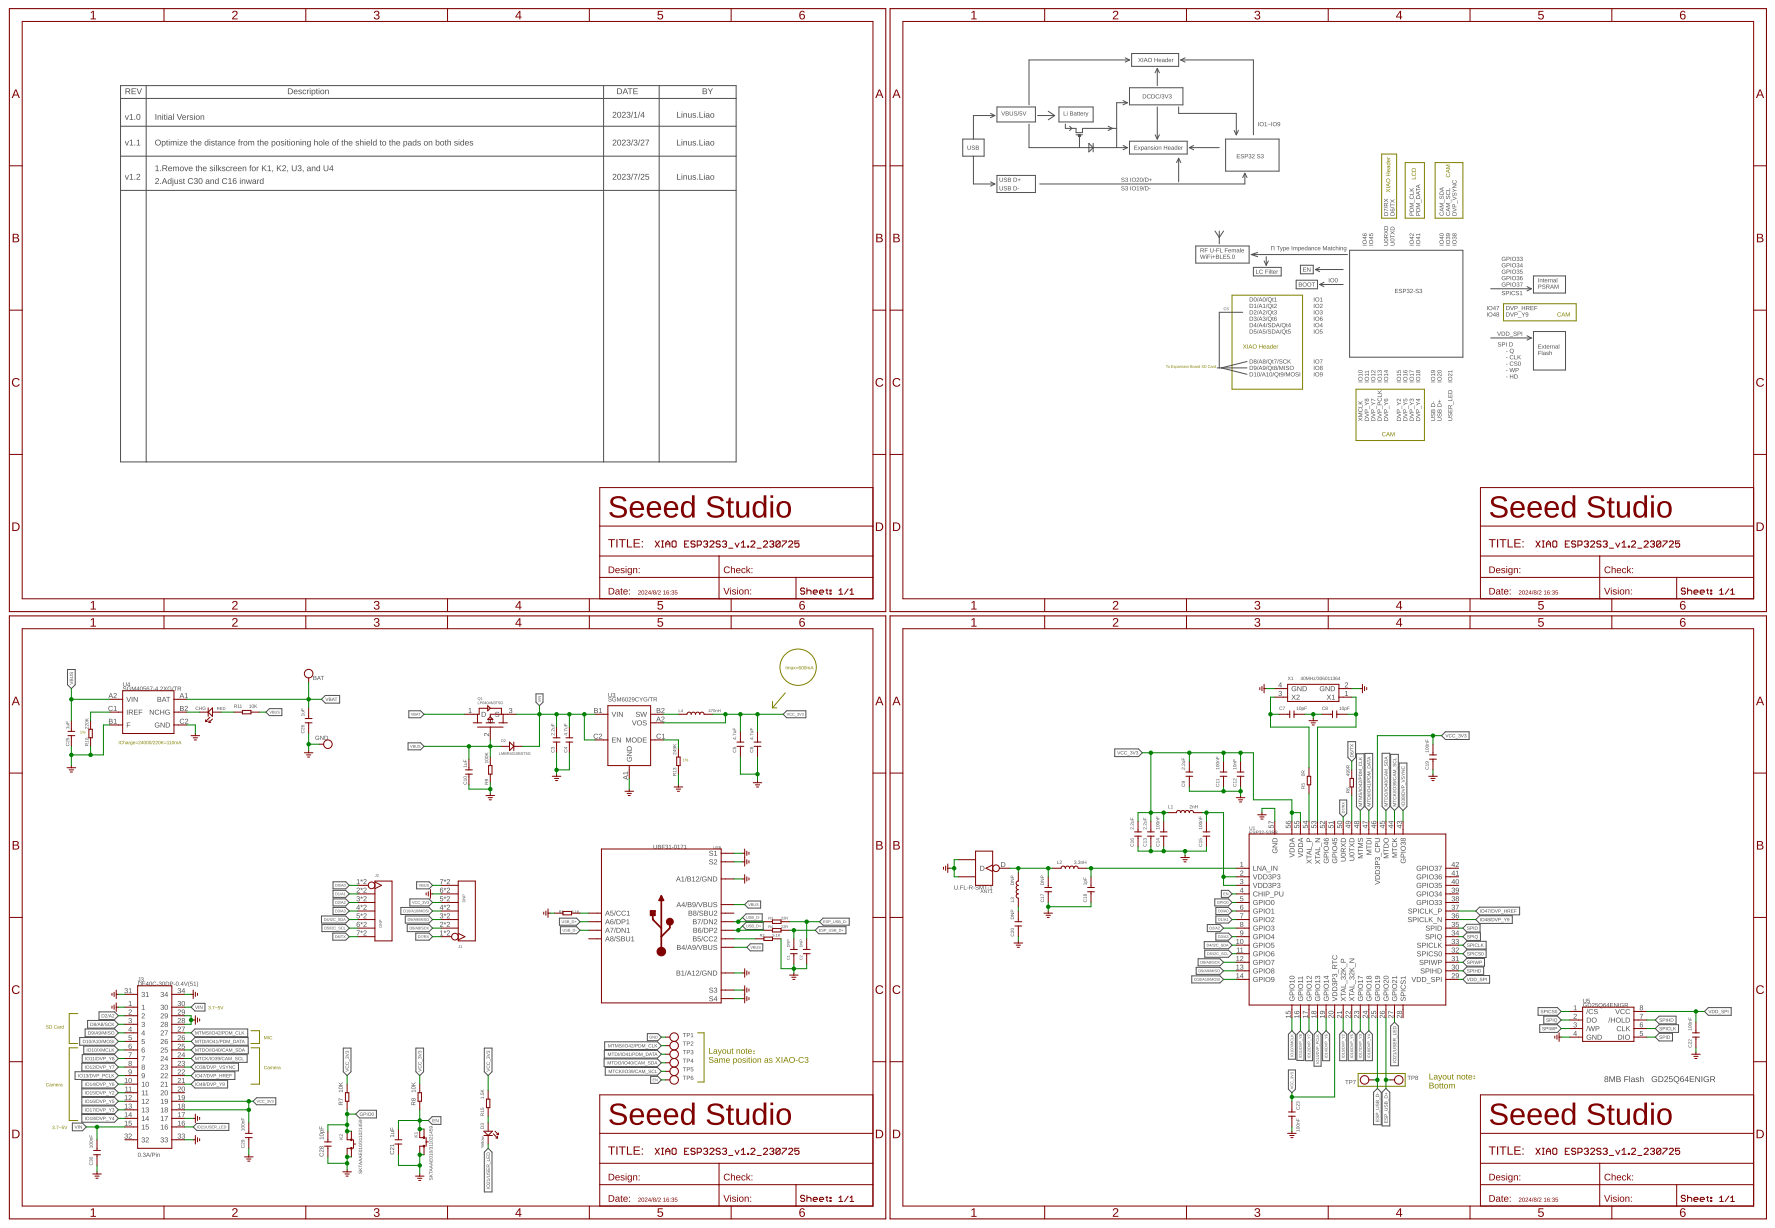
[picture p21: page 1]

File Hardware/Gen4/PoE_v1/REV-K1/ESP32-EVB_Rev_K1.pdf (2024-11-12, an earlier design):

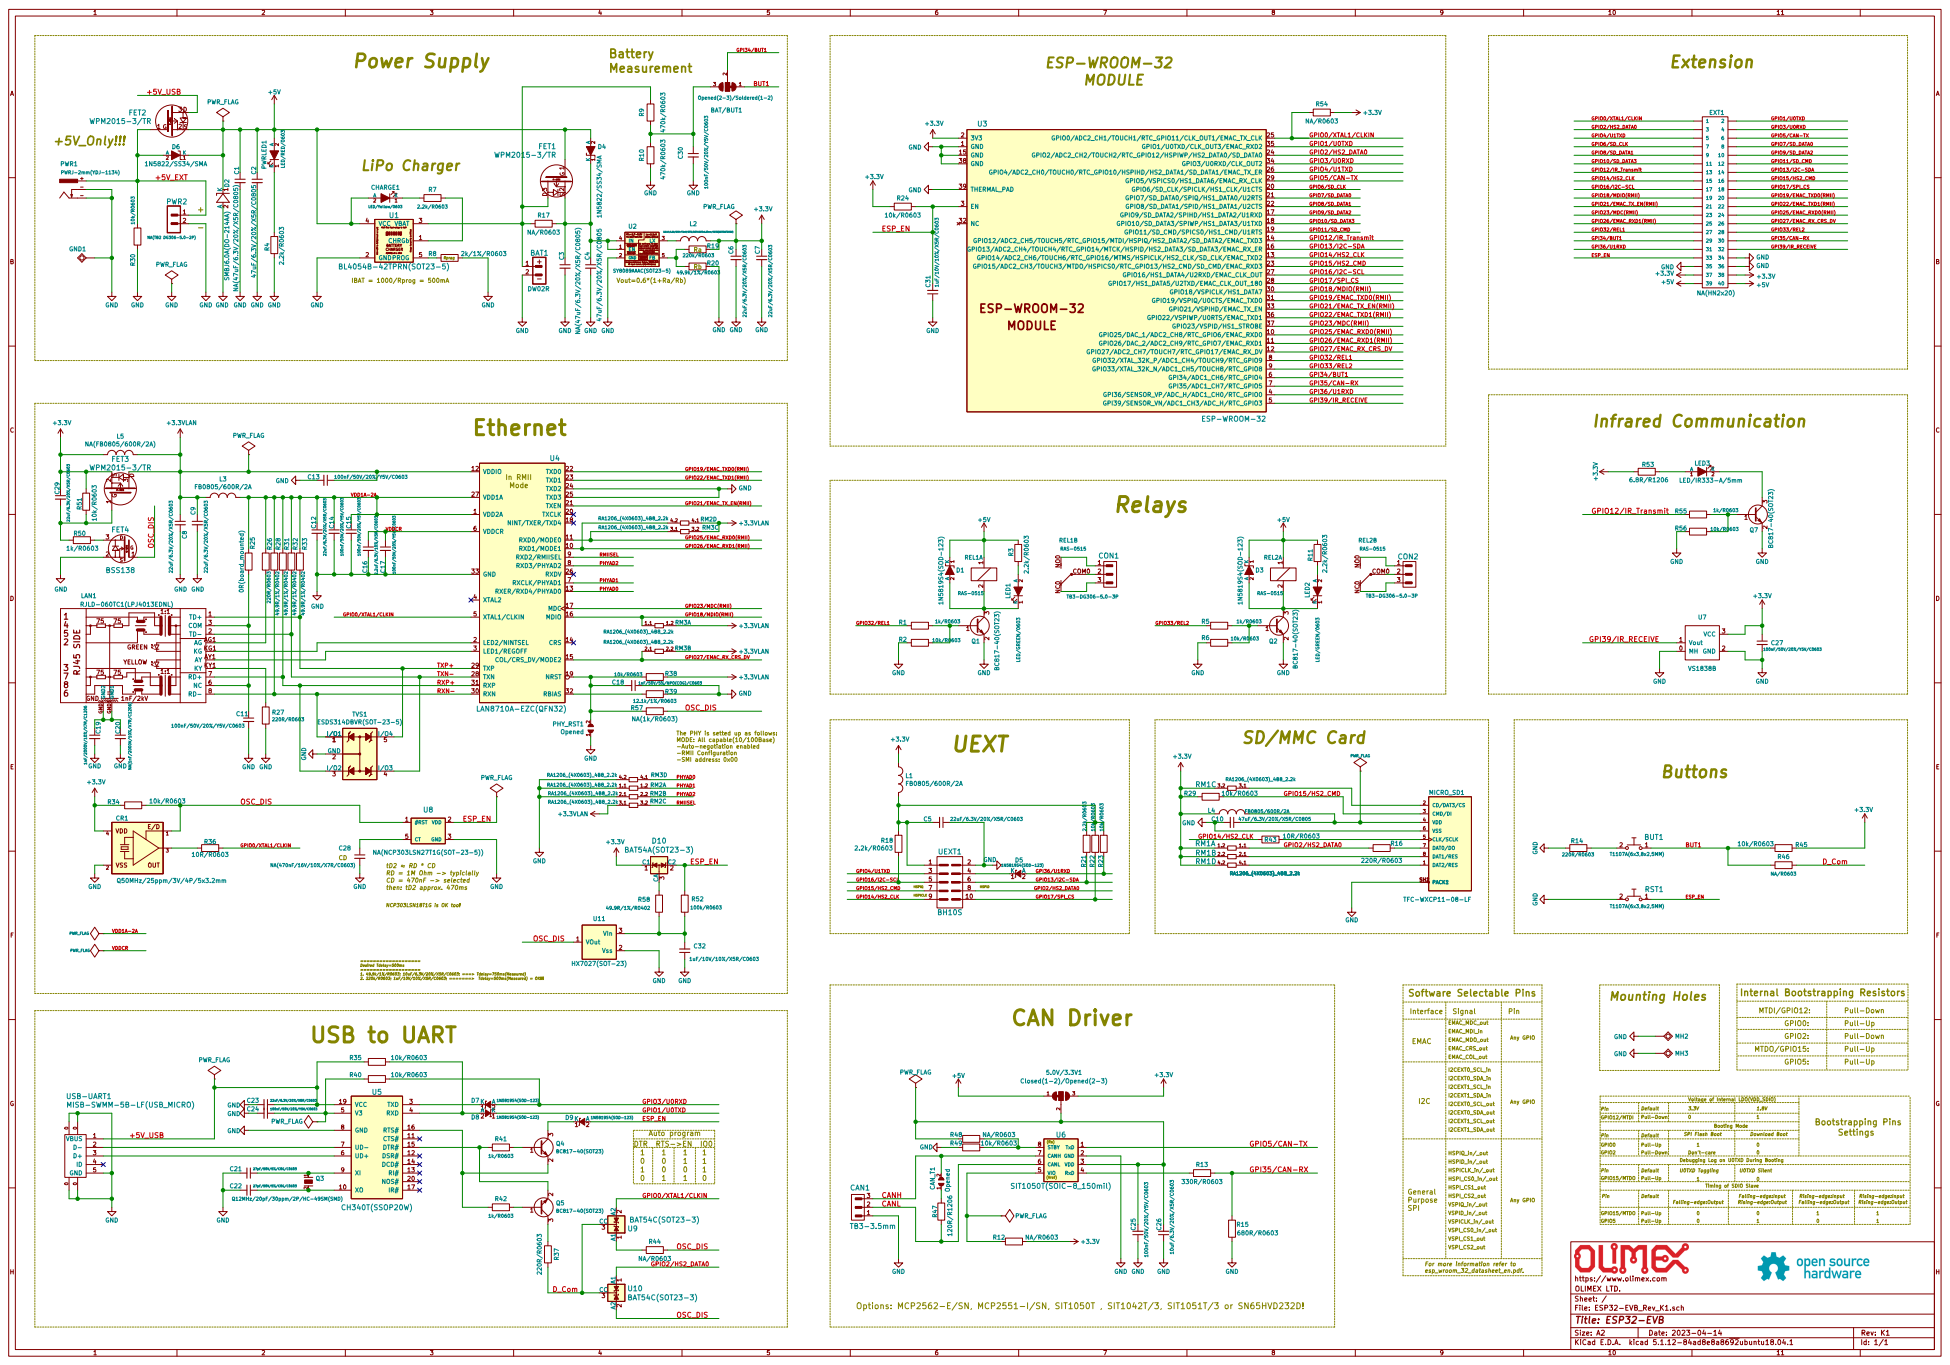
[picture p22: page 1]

Vout=0.6*(1+Ra/Rb) EN 1 GND 2

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

load current capability! Lx=2.2uH

ESP_EN GPIO19/EMAC_TXD0(RMII) RXN- RXP+ TXN- TXP+ OSC_DIS
PWR_FLAG

GPIO22/EMAC_TXD1(RMII) GPIO21/EMAC_TX_EN(RMII) GPIO25/EMAC_RXD0(RMII) GPIO25/EMAC_RXD0(RMII) GPIO18/MDIO(RMII) GPIO27/EMAC_RX_CRS_DV

1 2PHY_RST1 Opened C18 1nF/50V/5%/NPO(COG)/C0603 R39 GND

The PHY is setted up as follows: MODE: All capable(10/100Base)
-Auto-negotiation enabled
-RMII Configuration
2 CA3 D10 BAT54A(SOT23-3) GND

RD = 1M Ohm -> typiclally CD = 470nF -> selected

then: tD2 approx. 470ms USB to UART

Voltage of Internal LDO(VDD_SDIO) Signal Software Selectable Pins

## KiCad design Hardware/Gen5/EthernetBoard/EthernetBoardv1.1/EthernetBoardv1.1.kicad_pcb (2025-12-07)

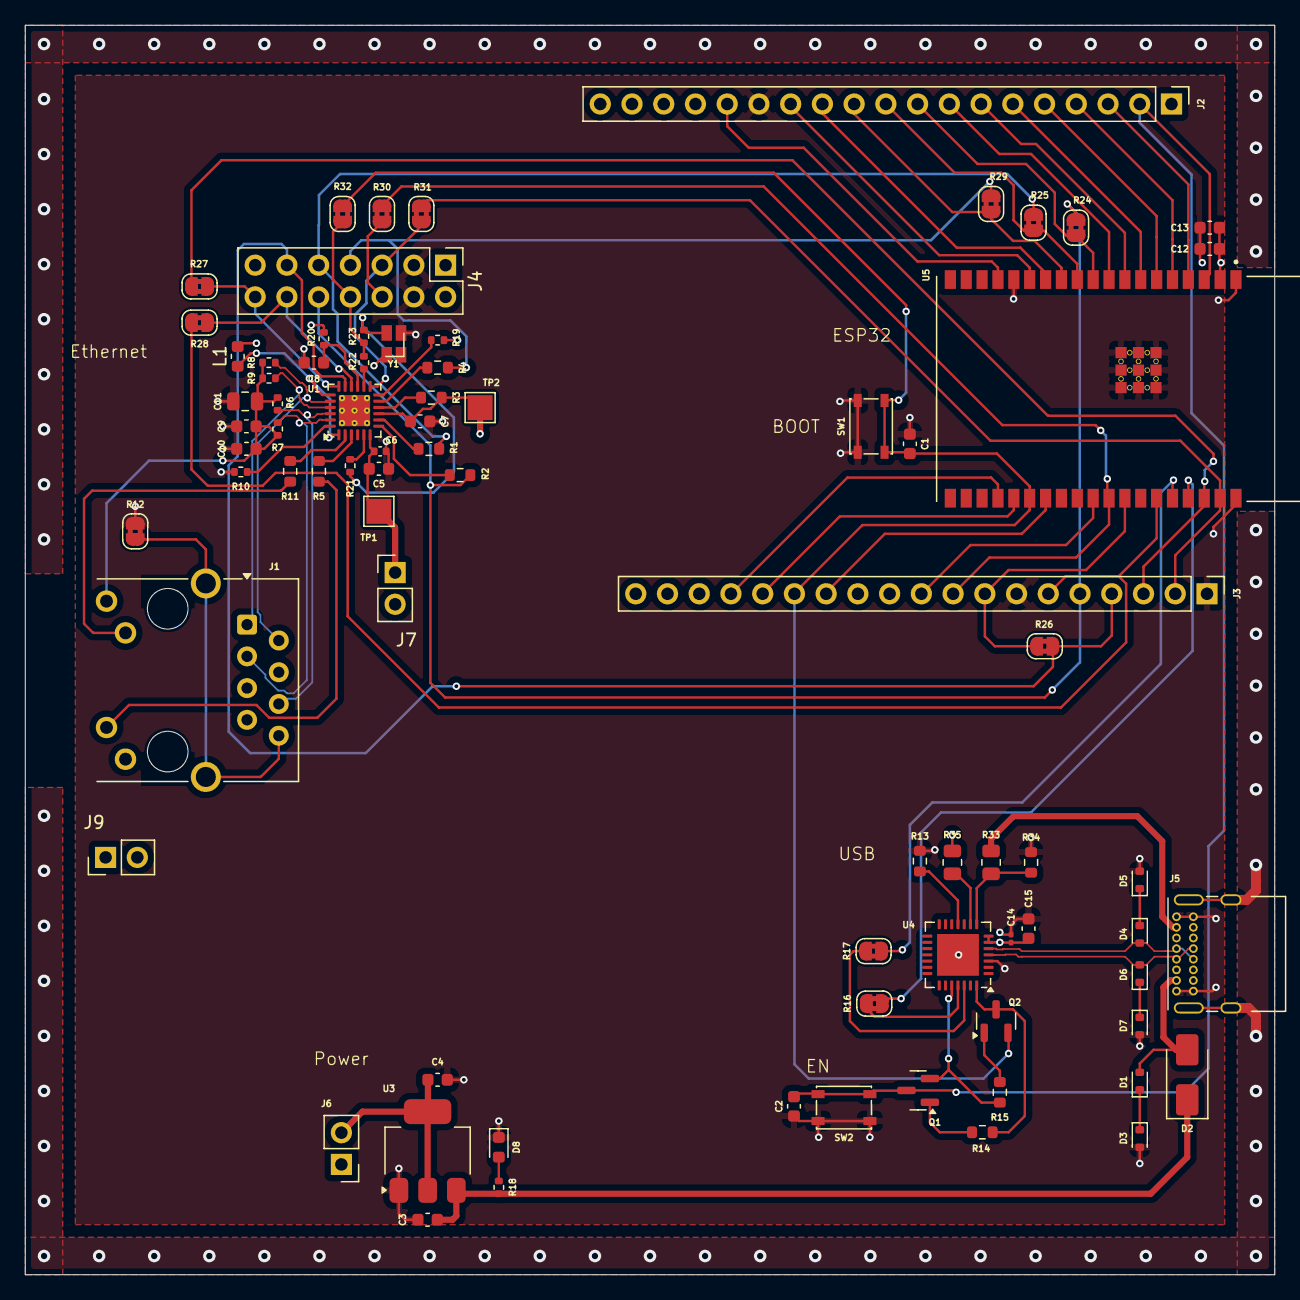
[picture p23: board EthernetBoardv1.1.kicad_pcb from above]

Board: 4 copper layers, 100.0 x 100.0 mm, 78 parts (0 on the bottom side), 76 nets.

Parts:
C1, C2, C7, C8, C9, C10, C13, C15: 0.1uF; C_0603_1608Metric
C3, C4, C12: 22uF; C_0603_1608Metric
C5: 470pF; C_0603_1608Metric
C6: 1uF; C_0402_1005Metric
C11: 0.022uF; C_0805_2012Metric
C14: 4.7uF; R_0201_0603Metric
D1, D3, D4, D5, D6, D7: ESD5Zxx; D_SOD-523
D2: B130-E3; D_SMA
D8: LED; LED_0603_1608Metric
J1: RJ45_Wuerth_7499010211A; RJ45_Wuerth_7499010211A_Horizontal
J2, J3: Conn_01x19_Pin; PinHeader_1x19_P2.54mm_Vertical
J4: Conn_02x07_Odd_Even; PinHeader_2x07_P2.54mm_Vertical
J5: USB_C_Receptacle_USB2.0_16P; USB_C_Receptacle_GCT_USB4085
J6, J7, J9: Conn_01x02_Pin; PinHeader_1x02_P2.54mm_Vertical
L1: L; L_0603_1608Metric
Q1, Q2: SS8050; SOT-23
R1, R2, R3, R4: 10R; R_0603_1608Metric
R5, R11: 332R; R_0603_1608Metric
R6, R7, R8, R9: 49.9R; R_0402_1005Metric
R10: 12.5K; R_0402_1005Metric
R12, R16, R17, R24, R25, R26, R27, R28, R29, R30, R31, R32: 0R; SolderJumper-2_P1.3mm_Bridged2Bar_RoundedPad1.0x1.5mm
R13, R14, R15: 10K; R_0603_1608Metric
R18: 2K; R_0402_1005Metric
R19: 1.5K; R_0402_1005Metric
R20: 4.7K; R_0402_1005Metric
R21, R22, R23: 33R; R_0402_1005Metric
R33: 22.1K; R_0805_2012Metric
R34: 47.5K; R_0603_1608Metric
R35: 2K; R_0805_2012Metric
SW1, SW2: SW_Push; SW_SPST_PTS810
TP1, TP2: TestPoint; TestPoint_Pad_2.0x2.0mm
U1: LAN8720A; VQFN-24-1EP_4x4mm_P0.5mm_EP2.5x2.5mm_ThermalVias
U3: AMS1117-3.3; SOT-223-3_TabPin2
U4: CP2102N-Axx-xQFN28; QFN-28-1EP_5x5mm_P0.5mm_EP3.35x3.35mm
U5: ESP32-WROVER-E-N8R8; XCVR_ESP32-WROVER-E-N8R8
Y1: ASCO; Oscillator_SMD_Abracon_ASCO-4Pin_1.6x1.2mm

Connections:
+3.3V: C4.1, C12.1, C13.1, C14.1, C15.1, J2.1, J6.2, J7.2, J9.2, R35.1, U3.2 (VO), U4.6 (VDD), U4.7 (VREGIN), U5.2 (3V3)
+5V: C3.1, D2.1 (K), R18.1, U3.3 (VI)
/CLK50: R21.2, R23.1, Y1.3 (OUT)
/CRS_DV: J4.7, R4.2, R29.2
/DTR: Q2.3 (C), R14.1, U4.28 (~DTR)
/EN: C2.2, J2.2, Q1.3 (C), SW2.2, U5.3 (EN)
/IO0: C1.2, J3.14, Q2.2 (E), R32.1, SW1.2, U5.25 (IO0)
/IO2: J3.15, U5.24 (IO2)
/IO4: J3.13, U5.26 (IO4)
/IO5: J3.10, U5.29 (IO5)
/IO12: J2.13, U5.14 (IO12)
/IO13: J2.15, U5.16 (IO13)
/IO14: J2.12, U5.13 (IO14)
/IO15: J3.16, U5.23 (IO15)
/IO18: J3.9, R30.1, U5.30 (IO18)
/IO19: J3.8, R26.1, U5.31 (IO19)
/IO21: J3.6, R28.1, U5.33 (IO21)
/IO22: J3.3, R27.1, U5.36 (IO22)
/IO23: J3.2, R31.1, U5.37 (IO23)
/IO25: J2.9, R24.1, U5.10 (IO25)
/IO26: J2.10, R25.1, U5.11 (IO26)
/IO27: J2.11, R29.1, U5.12 (IO27)
/IO32: J2.7, U5.8 (IO32)
/IO33: J2.8, U5.9 (IO33)
/IO34: J2.5, U5.6 (IO34)
/IO35: J2.6, U5.7 (IO35)
/LED1: R5.1, U1.3 (LED1/REGOFF)
/LED2: R11.1, U1.2 (LED2/~INTSEL)
/MDC: J4.5, R31.2, U1.13 (MDC)
/MDIO: J4.6, R30.2
/OSCIN: R21.1, U1.5 (XTAL1/CLKIN)
/RD_N: J1.6 (RD-), R6.2, U1.22 (RXN)
/RD_P: J1.3 (RD+), R7.2, U1.23 (RXP)
/REFCLKO: R22.1, U1.14 (~INT/REFCLKO)
/RTS: Q1.2 (E), R15.1, U4.24 (~RTS)
/RXD: R16.2, U4.25 (RXD)
/RXD0: J3.5, J4.10, R2.2, R24.2
/RXD1: J4.9, R1.1, R25.2
/RXDUSB: R17.1, U5.34 (RXD0)
/RXER: R3.1, U1.10 (RXER/PHYAD0)
/R_RX_CLK: J4.8, R22.2, R23.2, R32.2
/SENSOR_VN: J2.4, U5.5 (SENSOR_VN)
/SENSOR_VP: J2.3, U5.4 (SENSOR_VP)
/TD_N: J1.2 (TD-), R8.2, U1.20 (TXN)
/TD_P: J1.1 (TD+), R9.2, U1.21 (TXP)
/TXD: R17.2, U4.26 (TXD)
/TXD0: J3.4, J4.11, R26.2, U1.17 (TXD0)
/TXD1: J4.14, R27.2, U1.18 (TXD1)
/TXDUSB: R16.1, U5.35 (TXD0)
/TX_EN: J4.12, R28.2, U1.16 (TXEN)
/USB_DN: D4.2 (A), J5.A7 (D-), J5.B7 (D-), U4.5 (D-)
/USB_DP: D6.2 (A), J5.A6 (D+), J5.B6 (D+), U4.4 (D+)
/nRST: C8.1, R20.1, U1.15 (~RST)
GND: C1.1, C2.1, C3.2, C4.2, C5.2, C6.2, C7.2, C8.2, C9.2, C10.2, C11.2, C12.2, C13.2, C14.2, C15.2, D3.2 (A), D5.2 (A), D7.2 (A), D8.1 (K), J2.14, J3.1, J3.7, J4.3, J4.4, J5.A1 (GND), J5.A12 (GND), J5.B1 (GND), J5.B12 (GND), R10.2, R12.2, R13.2, R34.1, SW1.1, SW2.1, U1.25 (VSS), U3.1 (GND), U4.3 (GND), U4.29 (GND), U5.1 (GND), U5.15 (GND), U5.38 (GND), U5.39_1 (EXP), U5.39_2 (EXP), U5.39_3 (EXP), U5.39_4 (EXP), U5.39_5 (EXP), U5.39_6 (EXP), U5.39_7 (EXP), U5.39_8 (EXP), U5.39_9 (EXP), Y1.2 (GND)
unnamed: D1.1 (K), D3.1 (K)
unnamed: D4.1 (K), D5.1 (K)
unnamed: D6.1 (K), D7.1 (K)
unnamed: D8.2 (A), R18.2
unnamed: J1.8, J1.SH, R12.1
unnamed: J1.10, R11.2
unnamed: J1.11, R5.2
unnamed: Q1.1 (B), R14.2
unnamed: Q2.1 (B), R15.2
unnamed: R4.1, U1.11 (CRS_DV/MODE2)
unnamed: R19.1, U1.12 (MDIO)
unnamed: R10.1, U1.24 (RBIAS)
unnamed: R1.2, U1.8 (RXD0/MODE0)
unnamed: R2.1, U1.7 (RXD1/MODE1)
unnamed: L1.1, U1.1 (VDD2A), U1.19 (VDD1A)
unnamed: R33.2, R34.2, U4.8 (VBUS)
unnamed: R35.2, U4.9 (~RST)
unnamed: R13.1, U4.11 (~SUSPEND)
VBUS: D1.2 (A), D2.2 (A), J5.A4 (VBUS), J5.A9 (VBUS), J5.B4 (VBUS), J5.B9 (VBUS), R33.1
VCC: C7.1, J4.1, J4.2, J6.1, L1.2, R3.2, R19.2, R20.2, TP2.1, U1.9 (VDDIO), Y1.4 (VDD)
VDDA: C9.1, C10.1, C11.1, J1.4 (CTD), J1.5 (CRD), J1.9, J1.12, J9.1, R6.1, R7.1, R8.1, R9.1
VDDCR: C5.1, C6.1, J7.1, TP1.1, U1.6 (VDDCR)

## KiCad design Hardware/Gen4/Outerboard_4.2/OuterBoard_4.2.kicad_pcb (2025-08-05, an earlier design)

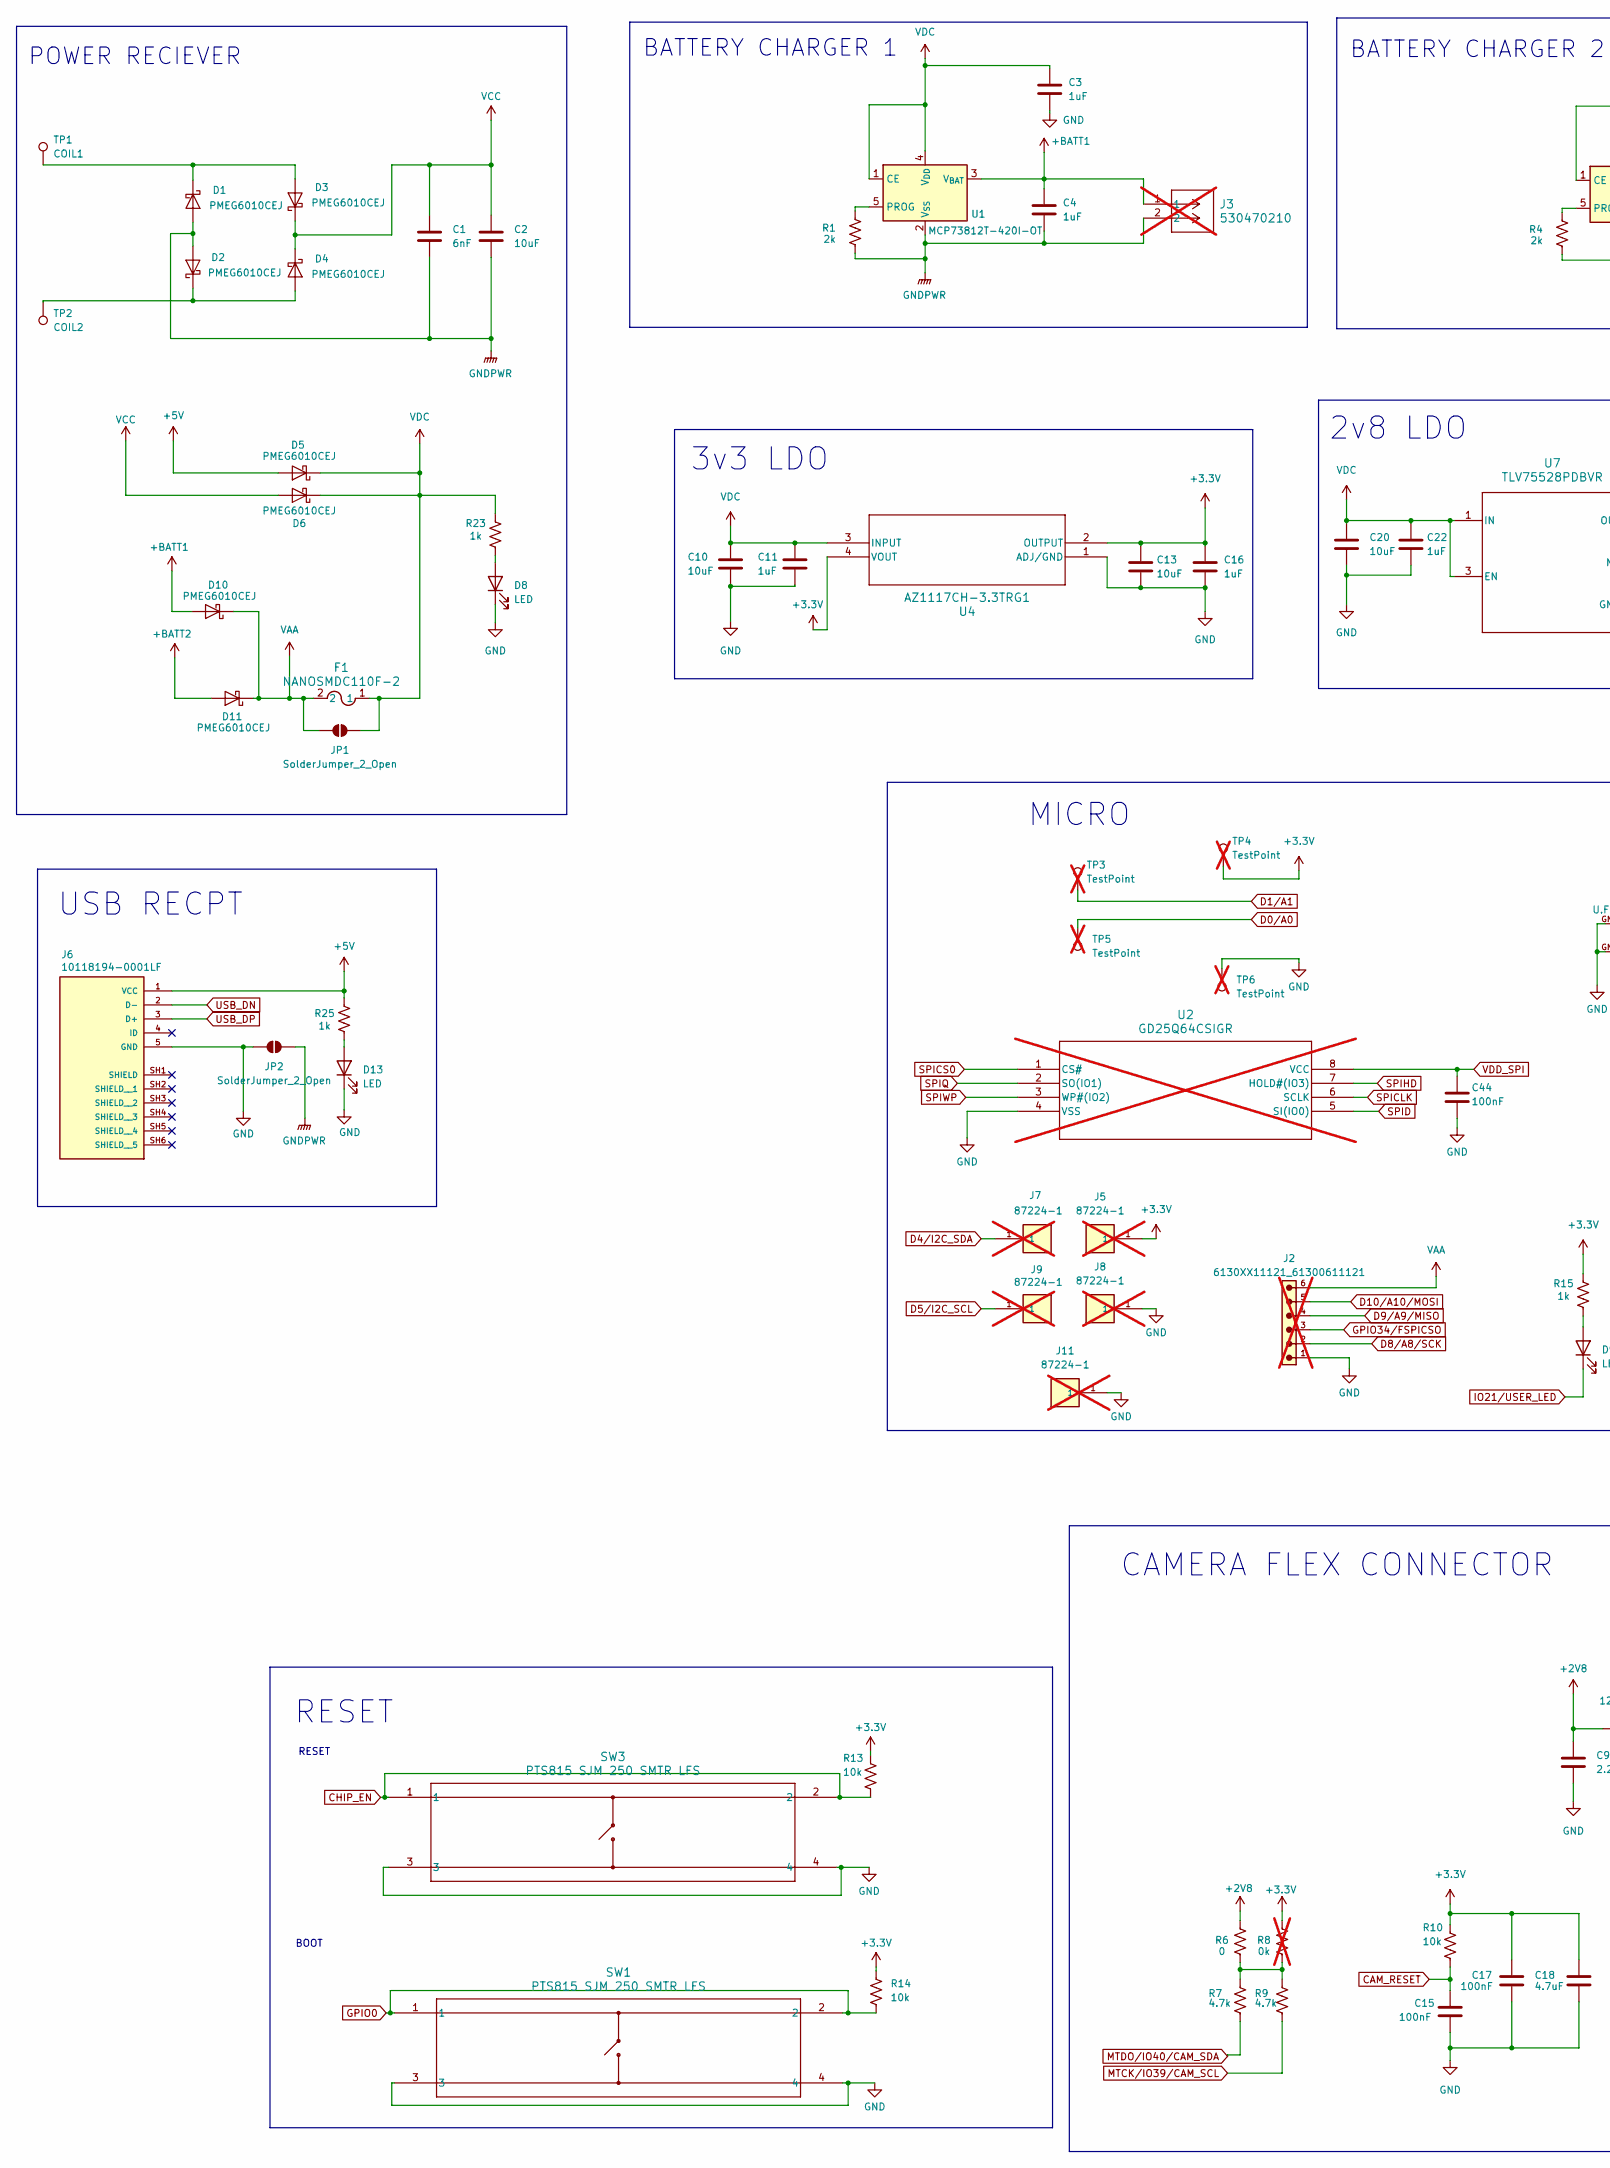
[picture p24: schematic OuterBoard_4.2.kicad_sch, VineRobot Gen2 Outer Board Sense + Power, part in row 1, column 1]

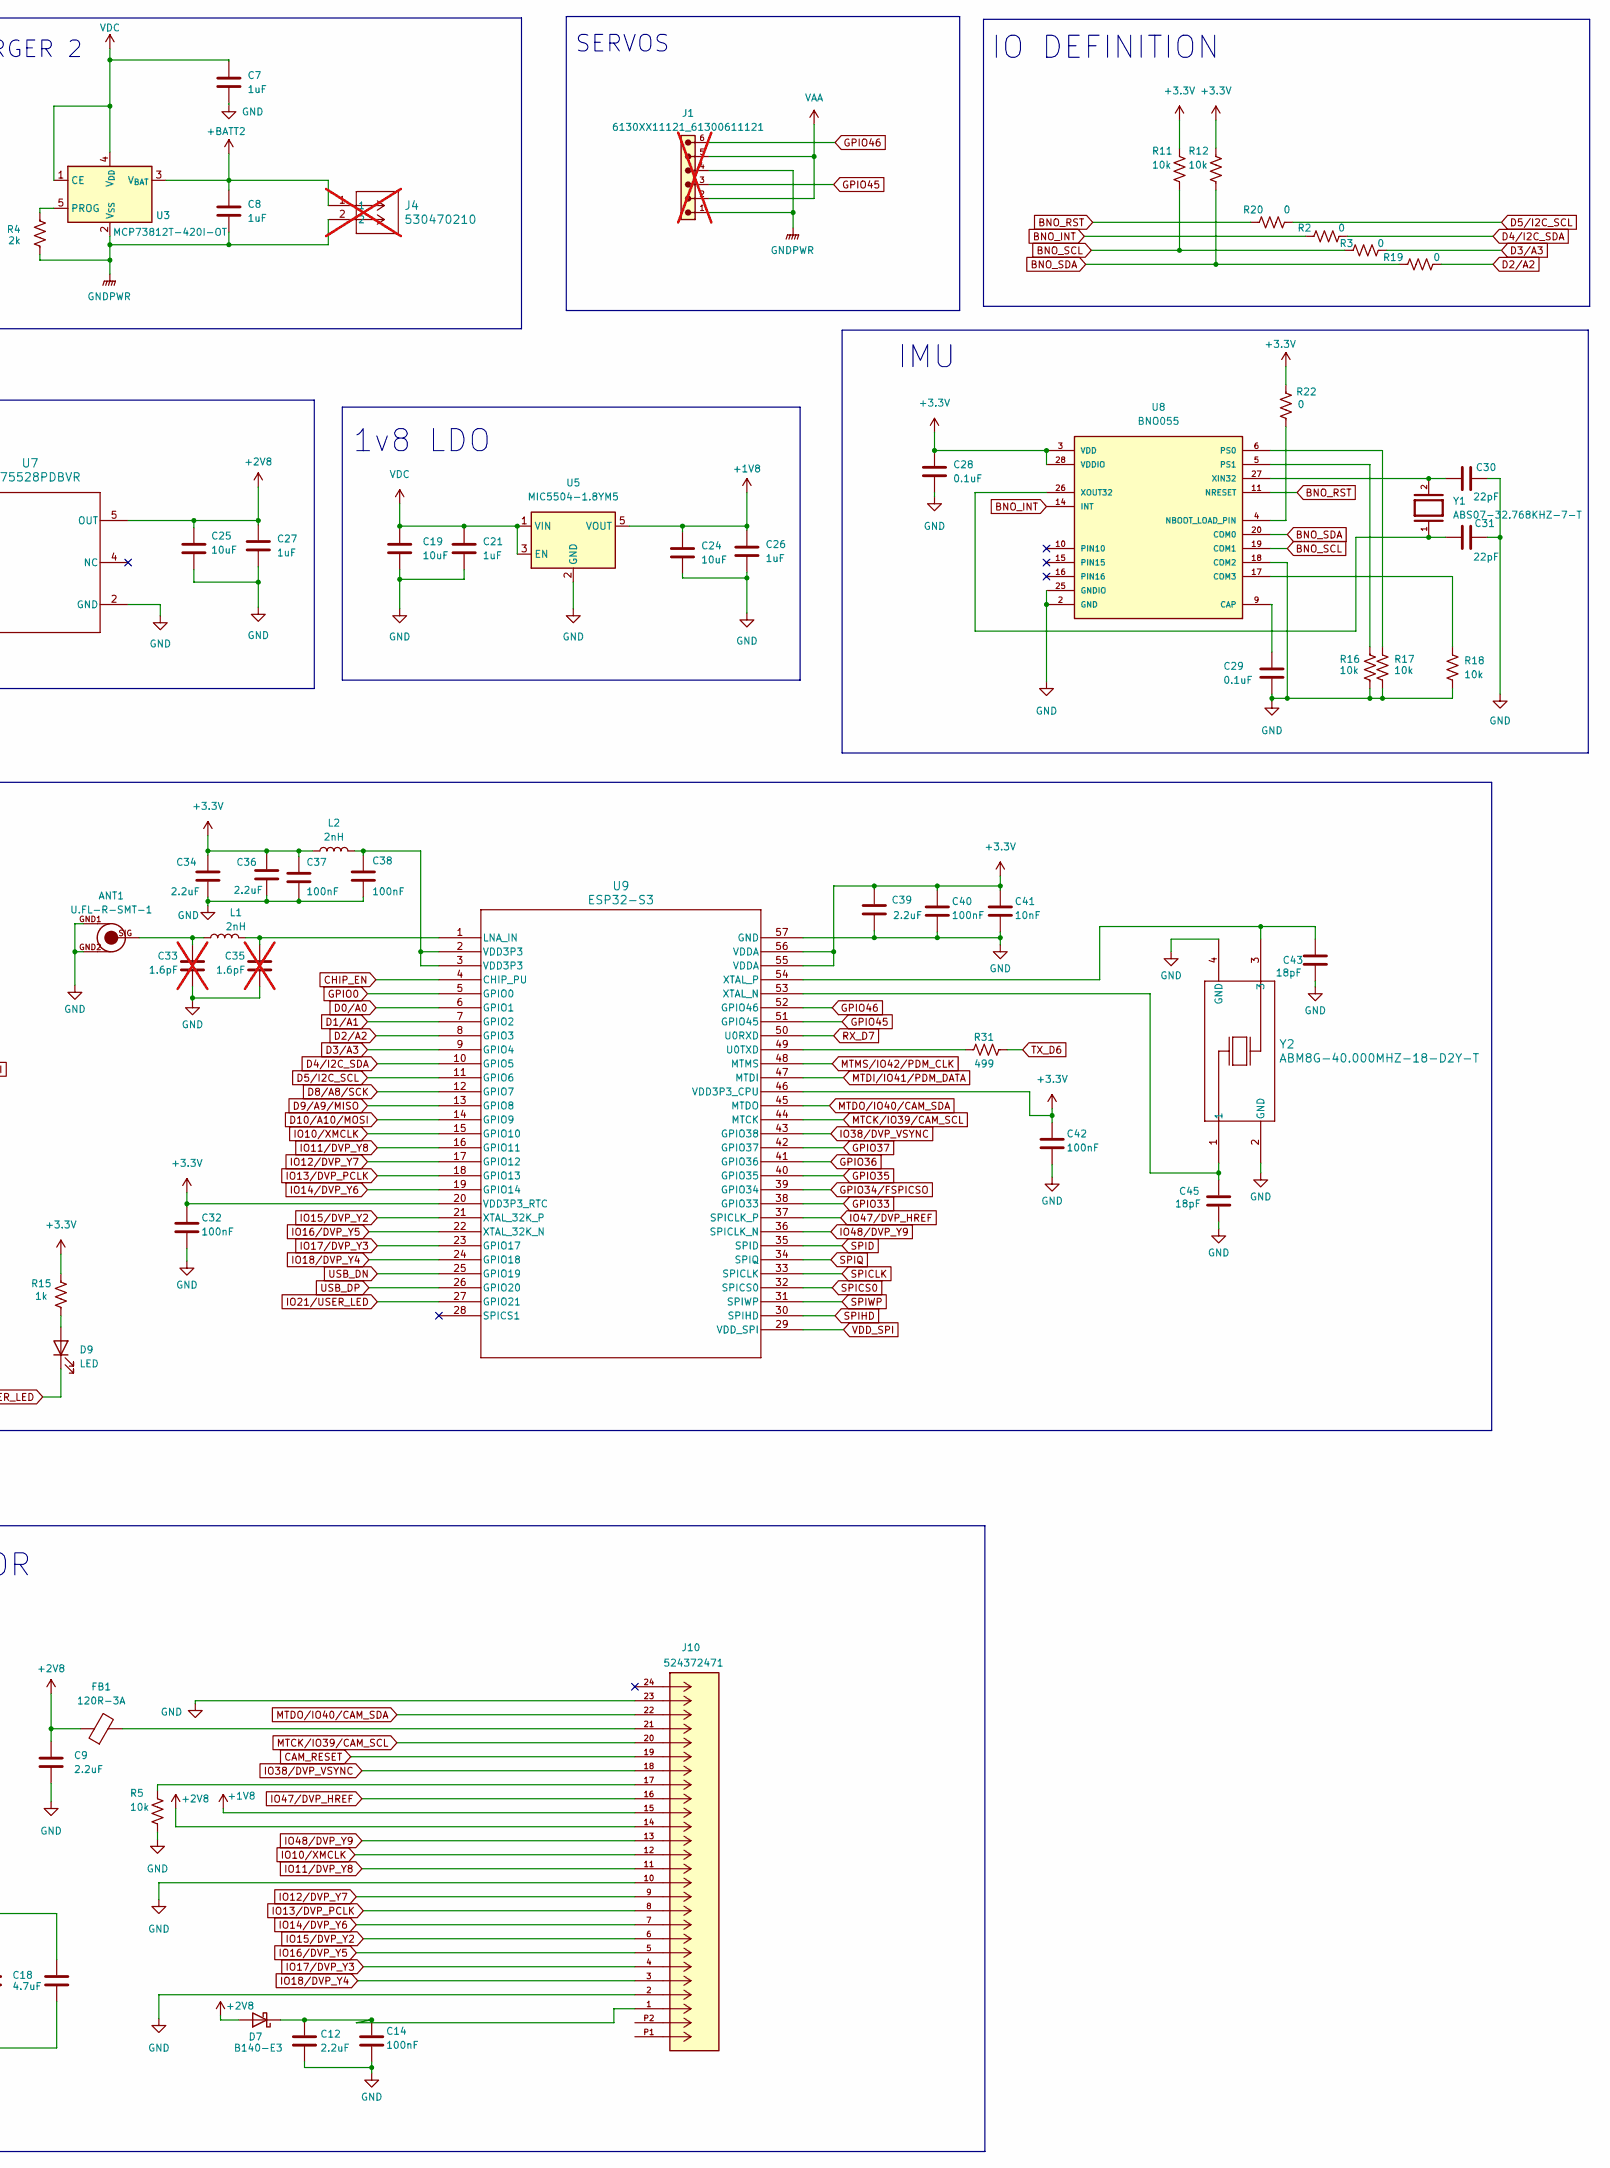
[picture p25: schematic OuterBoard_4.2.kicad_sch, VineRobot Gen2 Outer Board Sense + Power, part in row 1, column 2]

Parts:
ANT1: U.FL-R-SMT-1; Mfr P/N U.FL-R-SMT-1(10)
C1: 6nF; C_0805_2012Metric; Mfr P/N GRM2195C1H562JA01D
C2: 10uF; C_0402_1005Metric; Mfr P/N CL10A106KP8NNNC
C3, C4, C7, C8, C11, C16, C21, C22, C26, C27: 1uF; C_0603_1608Metric; Mfr P/N CC0201MRX5R6BB105
C9, C12, C34, C36, C39: 2.2uF; C_0603_1608Metric; Mfr P/N CL10A225KP8NNNC
C10, C13, C19, C20, C24, C25: 10uF; C_0603_1608Metric; Mfr P/N CL10A106MQ8NNNC
C14, C15, C17, C32, C37, C38, C40, C42, C44: 100nF; C_0603_1608Metric; Mfr P/N CL10B104KA8NNNC
C18: 4.7uF; C_0603_1608Metric; Mfr P/N CL10A475KP8NNNC
C28, C29: 0.1uF; C_0402_1005Metric; Mfr P/N CL05B104KO5NNNC
C30, C31: 22pF; C_0402_1005Metric; Mfr P/N GCM1555C1H220JA16D
C33, C35: 1.6pF; C_0402_1005Metric; Mfr P/N GJM1555C1H1R6WB01D; not fitted
C41: 10nF; C_0402_1005Metric; Mfr P/N 0402B103K500NT
C43, C45: 18pF; C_0201_0603Metric; Mfr P/N 0201CG180J500NT
D1, D2, D3, D4, D5, D6, D10, D11: PMEG6010CEJ; D_SOD-323F; Mfr P/N PMEG6010CEJ
D7: B140-E3; D_SMA; Mfr P/N B140-E3/61T
D8, D9, D13: LED; LED_0603_1608Metric; Mfr P/N KT-0603R
F1: NANOSMDC110F-2; FUS_NANO_TYCO_TYC; Mfr P/N NANOSMDC110F-2
FB1: 120R-3A; C_0805_2012Metric; Mfr P/N BLM21PG121SN1D
J1, J2: 6130XX11121_61300611121; 61300611121; PART-NUMBER 61300611121; not fitted
J3, J4: 530470210; CON_530470210_MOL; Mfr P/N 530470210; not fitted
J5, J7, J8, J9, J11: 87224-1; HDRV1W68P0_1X1_213X213X1036; PARTREV L3; not fitted
J6: 10118194-0001LF; AMPHENOL_10118194-0001LF; PARTREV D
J10: 524372471; CON_524372471_MOL; PARTREV C
JP1, JP2: SolderJumper_2_Open; SolderJumper-2_P1.3mm_Open_Pad1.0x1.5mm
L1: 2nH; L_0201_0603Metric; Mfr P/N LQP03TG2N0B02D
L2: 2nH; L_0402_1005Metric; Mfr P/N LQG15HS2N0B02D
R1, R4: 2k; R_0402_1005Metric; Mfr P/N 0402WGF2001TCE
R2, R3, R6, R19, R20, R22: 0; R_0402_1005Metric; Mfr P/N 0402WGJ0000TCE
R5, R11, R12, R16, R17, R18: 10k; R_0402_1005Metric; Mfr P/N 0402WGJ0103TCE
R7, R9: 4.7k; R_0402_1005Metric; Mfr P/N 0402WGF4701TCE
R8: 0k; R_0805_2012Metric; Mfr P/N RC0201FR-070RL; not fitted
R10: 10k; R_0805_2012Metric; Mfr P/N 0805W8F1002T5E
R13, R14: 10k; C_0402_1005Metric; Mfr P/N 0402WGJ0103TCE
R15, R23, R25: 1k; R_0402_1005Metric; Mfr P/N 0402WGF1001TCE
R31: 499; R_0402_1005Metric; Mfr P/N 0402WGF4990TCE
SW1, SW3: PTS815 SJM 250 SMTR LFS; SW4_PTS815 SJM 250 SMTR LFS_CNK; Mfr P/N PTS815SJG250SMTRLFS
TP1: COIL1; TestPoint_THTPad_2.0x2.0mm_Drill1.0mm
TP2: COIL2; TestPoint_THTPad_2.0x2.0mm_Drill1.0mm
TP3, TP4, TP5, TP6: TestPoint; PinHeader_1x01_P1.00mm_Vertical; not fitted
U1, U3: MCP73812T-420I-OT; SOT-23-5; Mfr P/N MCP73812T-420I/OT
U2: GD25Q64CSIGR; SOP8_208MIL_GDV; not fitted
U4: AZ1117CH-3.3TRG1; SOT-223_DIO; Mfr P/N AZ1117CH-3.3TRG1
U5: MIC5504-1.8YM5; SOT-23-5; Mfr P/N MIC5504-1.8YM5-TR
U7: TLV75528PDBVR; DBV0005A_N; Mfr P/N TLV75528PDBVR
U8: BNO055; LGA28R50P4X10_380X520X100; Mfr P/N BNO055
U9: ESP32-S3; QFN-56-1EP_7x7mm_P0.4mm_EP3.2x3.2mm; Mfr P/N ESP32-S3R8
Y1: ABS07-32.768KHZ-7-T; XTAL_ABS07-32.768KHZ-7-T; PARTREV 08.19.15
Y2: ABM8G-40.000MHZ-18-D2Y-T; CRYSTAL_ABM8G_ABR; Mfr P/N ABM8G-40.000MHZ-18-D2Y-T

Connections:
+1V8: C24.1, C26.1, J10.15, U5.5 (VOUT)
+2V8: C9.1, C25.1, C27.1, D7.2 (A), FB1.1, J10.14, R6.2, U7.5 (OUT)
+3.3V: C13.1, C16.1, C17.1, C18.1, C28.1, C32.1, C34.1, C36.1, C37.1, C39.1, C40.1, C41.1, C42.1, J5.1, L2.1, R8.2, R10.1, R11.1, R12.1, R13.1, R14.1, R15.2, R22.1, TP4.1, U4.2 (OUTPUT), U4.4 (VOUT), U8.3 (VDD), U8.28 (VDDIO), U9.20 (VDD3P3_RTC), U9.46 (VDD3P3_CPU), U9.55 (VDDA), U9.56 (VDDA)
+5V: D5.2 (A), J6.1 (VCC), R25.2
+BATT1: C4.1, D10.2 (A), J3.1, U1.3 (V_{BAT})
+BATT2: C8.1, D11.2 (A), J4.1, U3.3 (V_{BAT})
BNO_INT: R2.2, U8.14 (INT)
BNO_RST: R20.2, U8.11 (NRESET)
BNO_SCL: R3.2, R11.2, U8.19 (COM1)
BNO_SDA: R12.2, R19.2, U8.20 (COM0)
CAM_RESET: C15.1, J10.19, R10.2
CHIP_EN: R13.2, SW3.1, SW3.2, U9.4 (CHIP_PU)
D0/A0: TP5.1, U9.6 (GPIO1)
D1/A1: TP3.1, U9.7 (GPIO2)
D2/A2: R19.1, U9.8 (GPIO3)
D3/A3: R3.1, U9.9 (GPIO4)
D4/I2C_SDA: J7.1, R2.1, U9.10 (GPIO5)
D5/I2C_SCL: J9.1, R20.1, U9.11 (GPIO6)
D8/A8/SCK: J2.2, U9.12 (GPIO7)
D9/A9/MISO: J2.4, U9.13 (GPIO8)
D10/A10/MOSI: J2.5, U9.14 (GPIO9)
GND: ANT1.GND1, ANT1.GND2, C3.2, C7.2, C9.2, C10.2, C11.2, C12.2, C13.2, C14.2, C15.2, C16.2, C17.2, C18.2, C19.2, C20.2, C21.2, C22.2, C24.2, C25.2, C26.2, C27.2, C28.2, C29.2, C30.2, C31.2, C32.2, C33.2, C34.2, C35.2, C36.2, C37.2, C38.2, C39.2, C40.2, C41.2, C42.2, C43.2, C44.2, C45.2, D8.1 (K), D13.1 (K), J2.1, J6.5 (GND), J8.1, J10.2, J10.10, J10.23, J11.1, JP2.1 (A), R5.2, R16.2, R17.2, R18.2, SW1.3, SW1.4, SW3.3, SW3.4, TP6.1, U2.4 (VSS), U4.1 (ADJ/GND), U5.2 (GND), U7.2 (GND), U8.2 (GND), U8.18 (COM2), U8.25 (GNDIO), U9.57 (GND), Y2.2 (GND), Y2.4 (GND)
GNDPWR: C1.2, C2.2, C4.2, C8.2, D1.2 (A), D2.2 (A), J1.1, J1.4, J3.2, J4.2, JP2.2 (B), R1.2, R4.2, U1.2 (V_{SS}), U3.2 (V_{SS})
GPIO0: R14.2, SW1.1, SW1.2, U9.5 (GPIO0)
GPIO33: U9.38 (GPIO33)
GPIO34/FSPICSO: J2.3, U9.39 (GPIO34)
GPIO35: U9.40 (GPIO35)
GPIO36: U9.41 (GPIO36)
GPIO37: U9.42 (GPIO37)
GPIO45: J1.3, U9.51 (GPIO45)
GPIO46: J1.6, U9.52 (GPIO46)
IO10/XMCLK: J10.12, U9.15 (GPIO10)
IO11/DVP_Y8: J10.11, U9.16 (GPIO11)
IO12/DVP_Y7: J10.9, U9.17 (GPIO12)
IO13/DVP_PCLK: J10.8, U9.18 (GPIO13)
IO14/DVP_Y6: J10.7, U9.19 (GPIO14)
IO15/DVP_Y2: J10.6, U9.21 (XTAL_32K_P)
IO16/DVP_Y5: J10.5, U9.22 (XTAL_32K_N)
IO17/DVP_Y3: J10.4, U9.23 (GPIO17)
IO18/DVP_Y4: J10.3, U9.24 (GPIO18)
IO21/USER_LED: D9.1 (K), U9.27 (GPIO21)
IO38/DVP_VSYNC: J10.18, U9.43 (GPIO38)
IO47/DVP_HREF: J10.16, U9.37 (SPICLK_P)
IO48/DVP_Y9: J10.13, U9.36 (SPICLK_N)
MTCK/IO39/CAM_SCL: J10.20, R9.2, U9.44 (MTCK)
MTDI/IO41/PDM_DATA: U9.47 (MTDI)
MTDO/IO40/CAM_SDA: J10.22, R7.2, U9.45 (MTDO)
MTMS/IO42/PDM_CLK: U9.48 (MTMS)
unnamed: ANT1.SIG, C33.1, L1.2
unnamed: C38.1, L2.2, U9.2 (VDD3P3), U9.3 (VDD3P3)
unnamed: D1.1 (K), D3.2 (A), TP1.1
unnamed: D2.1 (K), D4.2 (A), TP2.1
unnamed: C12.1, C14.1, D7.1 (K), J10.1
unnamed: D8.2 (A), R23.1
unnamed: D9.2 (A), R15.1
unnamed: D13.2 (A), R25.1
unnamed: FB1.2, J10.21
unnamed: J10.17, R5.1
unnamed: R6.1, R7.1, R8.1, R9.1
unnamed: R1.1, U1.5 (PROG)
unnamed: R4.1, U3.5 (PROG)
unnamed: C29.1, U8.9 (CAP)
unnamed: R18.1, U8.17 (COM3)
unnamed: R22.2, U8.4 (NBOOT_LOAD_PIN)
unnamed: R17.1, U8.6 (PS0)
unnamed: R16.1, U8.5 (PS1)
unnamed: C30.1, U8.27 (XIN32), Y1.2
unnamed: C31.1, U8.26 (XOUT32), Y1.1
unnamed: C35.1, L1.1, U9.1 (LNA_IN)
unnamed: R31.1, U9.49 (U0TXD)
unnamed: C45.1, U9.53 (XTAL_N), Y2.1
unnamed: C43.1, U9.54 (XTAL_P), Y2.3
RX_D7: U9.50 (U0RXD)
SPICLK: U2.6 (SCLK), U9.33 (SPICLK)
SPICS0: U2.1 (CS#), U9.32 (SPICS0)
SPID: U2.5 (SI(IO0)), U9.35 (SPID)
SPIHD: U2.7 (HOLD#(IO3)), U9.30 (SPIHD)
SPIQ: U2.2 (SO(IO1)), U9.34 (SPIQ)
SPIWP: U2.3 (WP#(IO2)), U9.31 (SPIWP)
TX_D6: R31.2
USB_DN: J6.2 (D-), U9.25 (GPIO19)
USB_DP: J6.3 (D+), U9.26 (GPIO20)
VAA: D10.1 (K), D11.1 (K), F1.2, J1.2, J1.5, J2.6, JP1.1 (A)
VCC: C1.1, C2.1, D3.1 (K), D4.1 (K), D6.2 (A)
VDC: C3.1, C7.1, C10.1, C11.1, C19.1, C20.1, C21.1, C22.1, D5.1 (K), D6.1 (K), F1.1, JP1.2 (B), R23.2, U1.1 (CE), U1.4 (V_{DD}), U3.1 (CE), U3.4 (V_{DD}), U4.3 (INPUT), U5.1 (VIN), U5.3 (EN), U7.1 (IN), U7.3 (EN)
VDD_SPI: C44.1, U2.8 (VCC), U9.29 (VDD_SPI)

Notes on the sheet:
CAMERA FLEX CONNECTOR
RESET
IMU
POWER RECIEVER
MICRO
1v8 LDO
USB RECPT
BOOT
SERVOS
BATTERY CHARGER 1
BATTERY CHARGER 2
IO DEFINITION
2v8 LDO
3v3 LDO

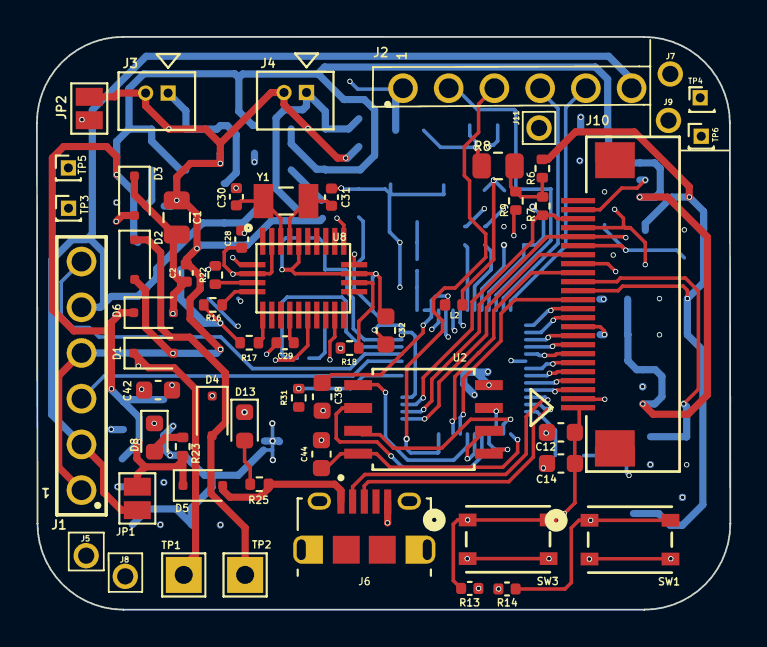
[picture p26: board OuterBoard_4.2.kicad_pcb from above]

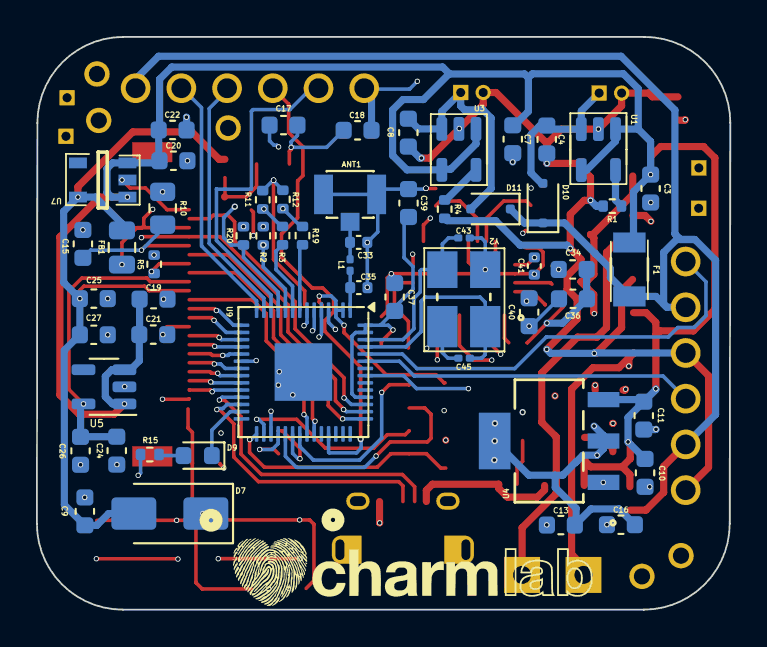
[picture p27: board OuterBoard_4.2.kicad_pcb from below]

Board: 6 copper layers, 38.5 x 31.8 mm, 114 parts (56 on the bottom side), 78 nets.

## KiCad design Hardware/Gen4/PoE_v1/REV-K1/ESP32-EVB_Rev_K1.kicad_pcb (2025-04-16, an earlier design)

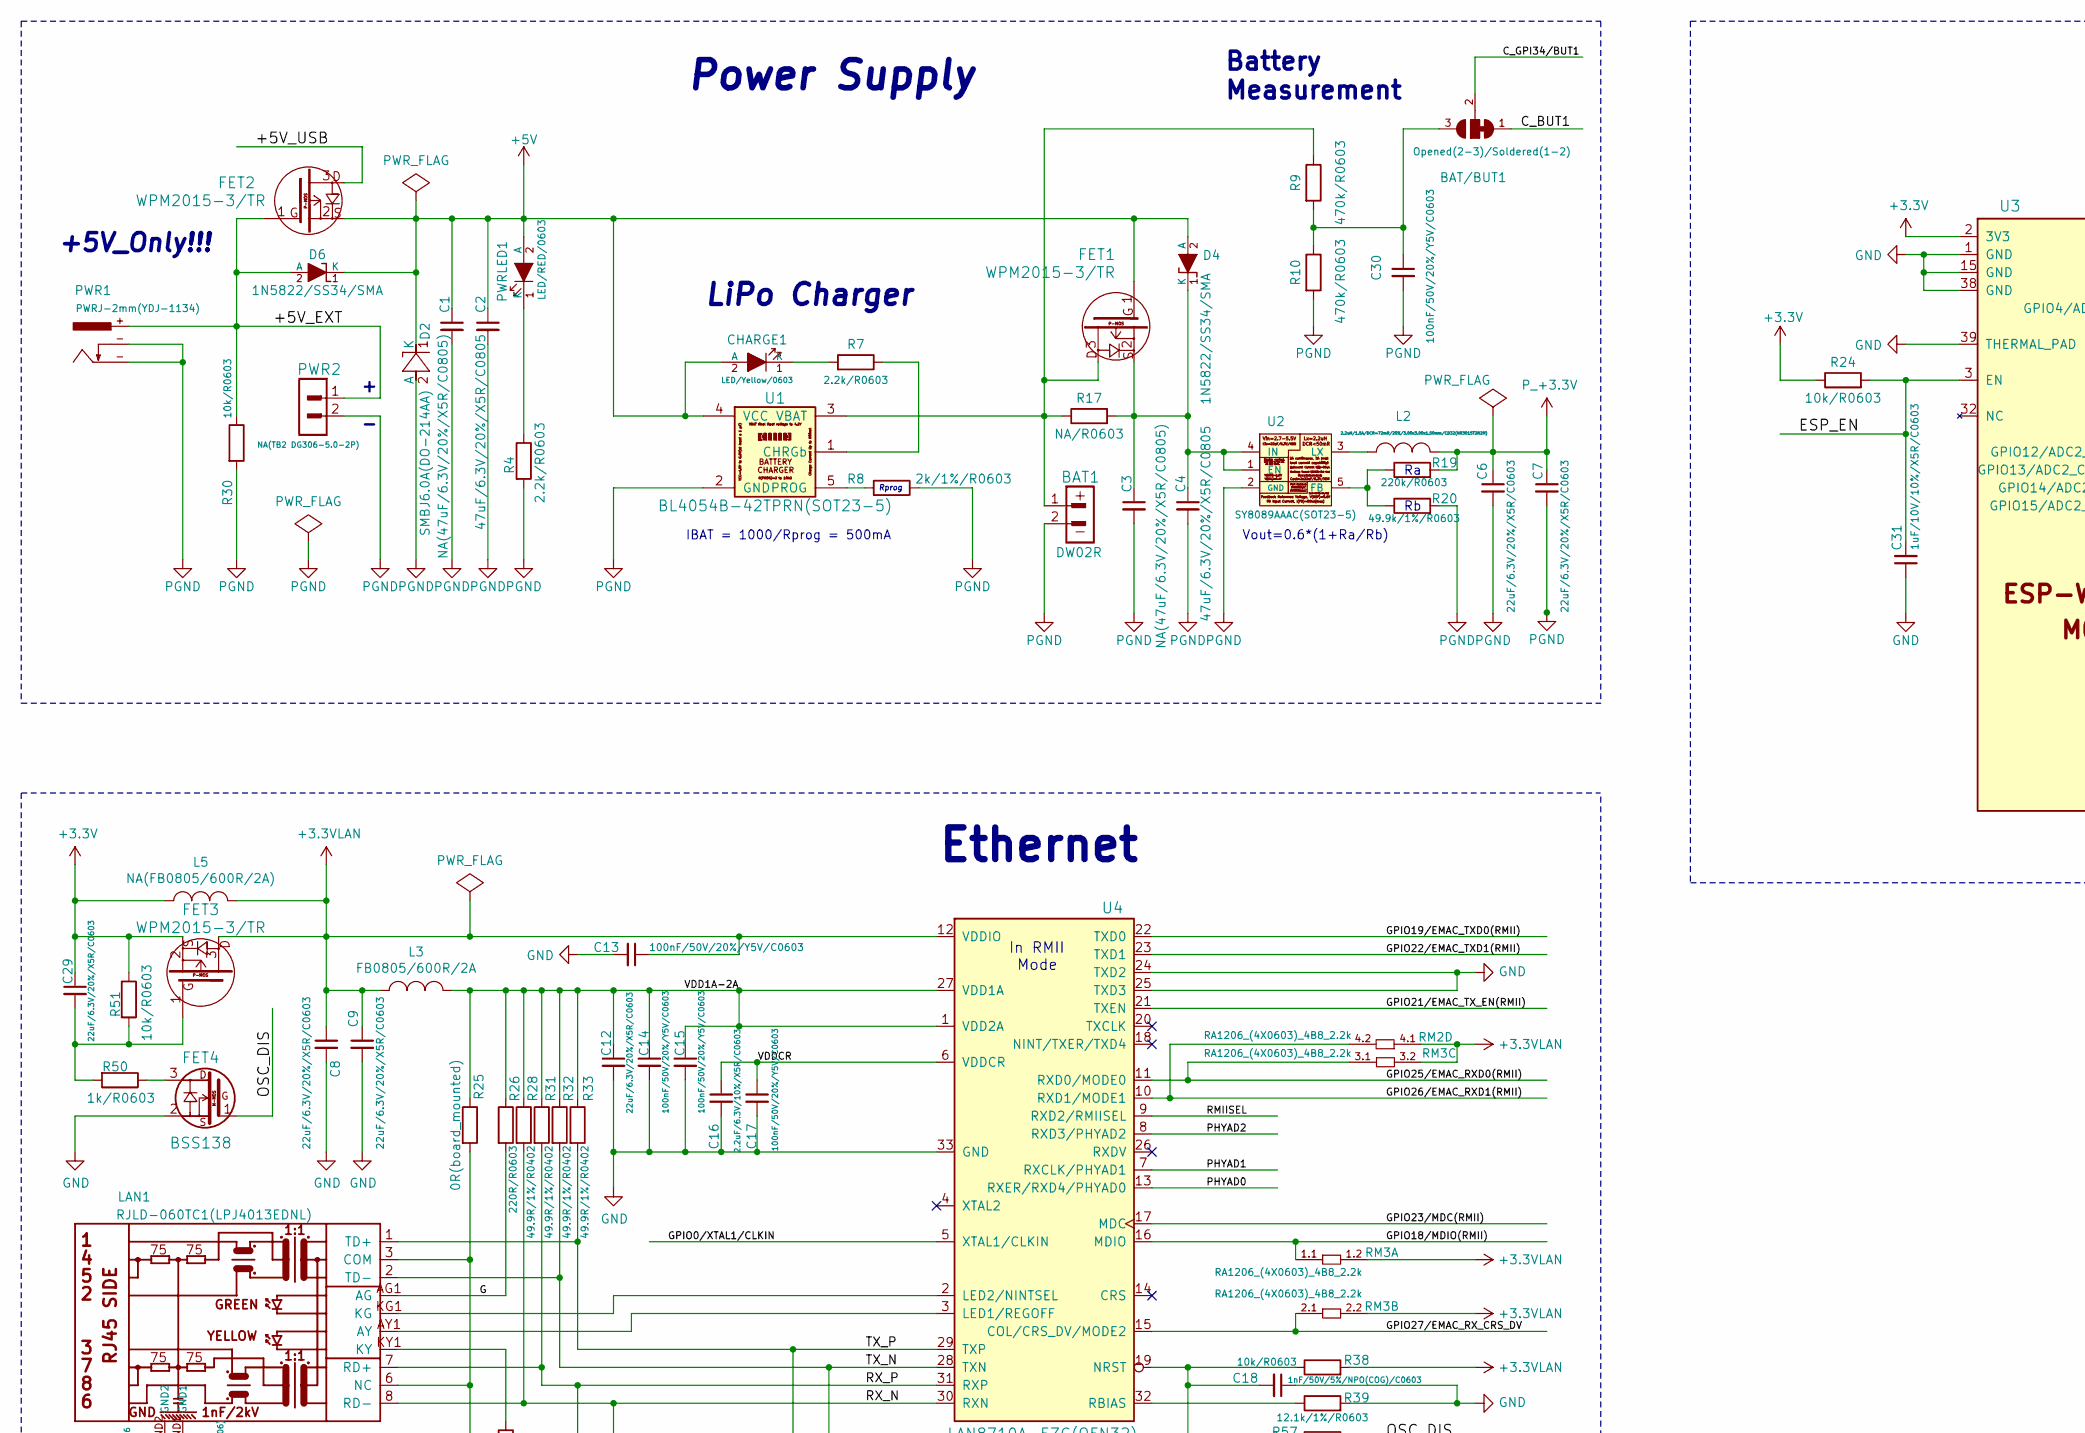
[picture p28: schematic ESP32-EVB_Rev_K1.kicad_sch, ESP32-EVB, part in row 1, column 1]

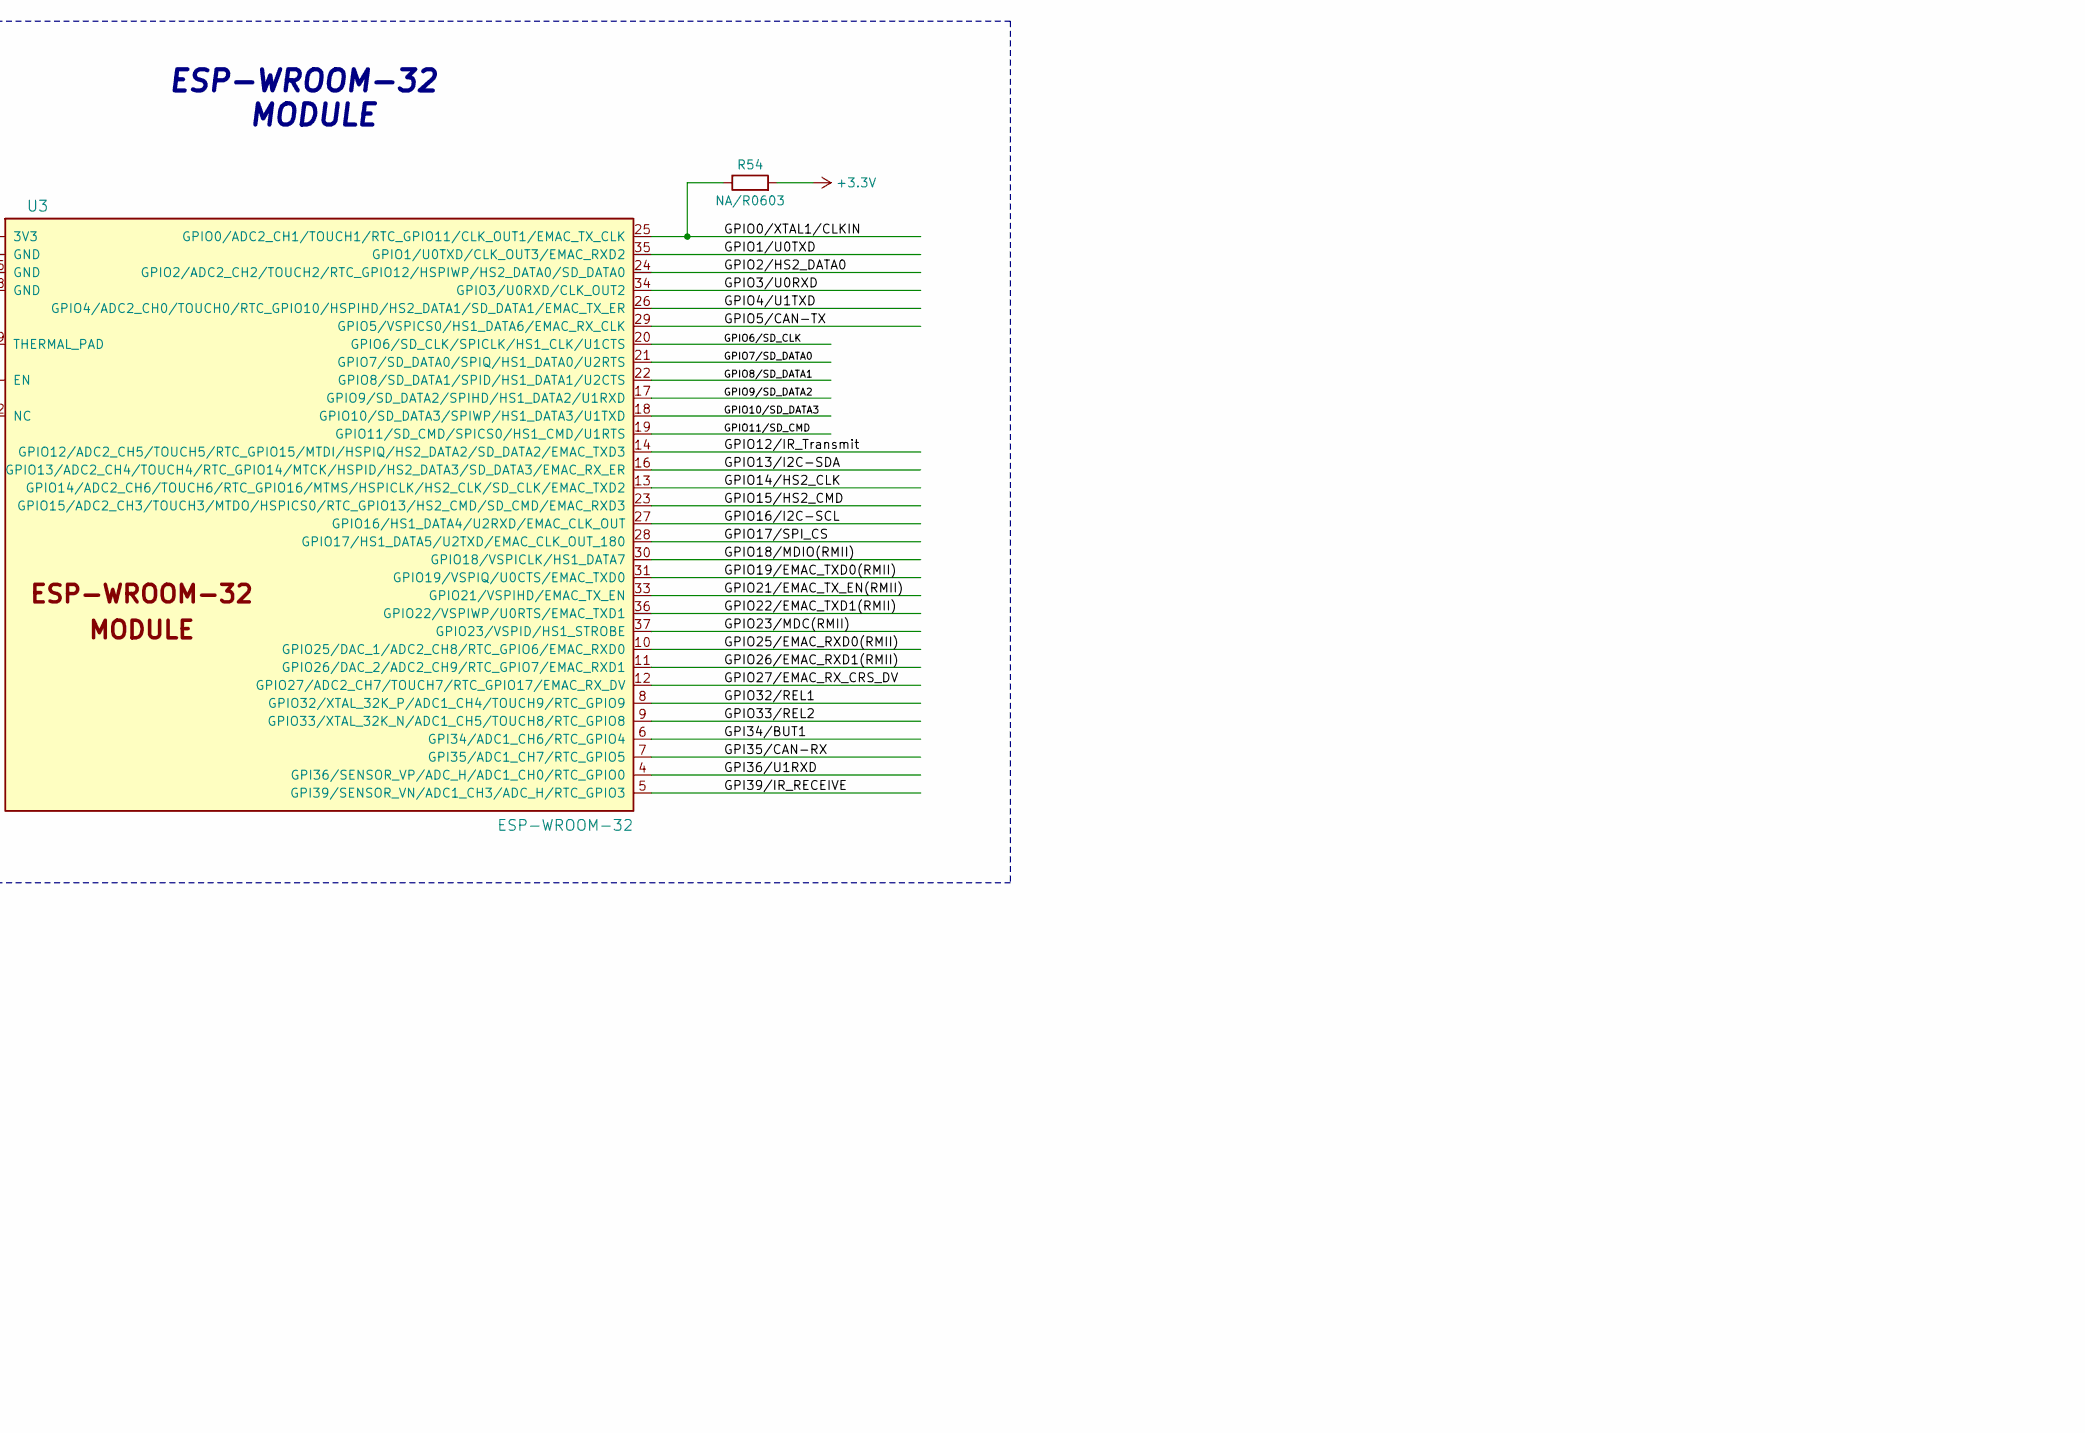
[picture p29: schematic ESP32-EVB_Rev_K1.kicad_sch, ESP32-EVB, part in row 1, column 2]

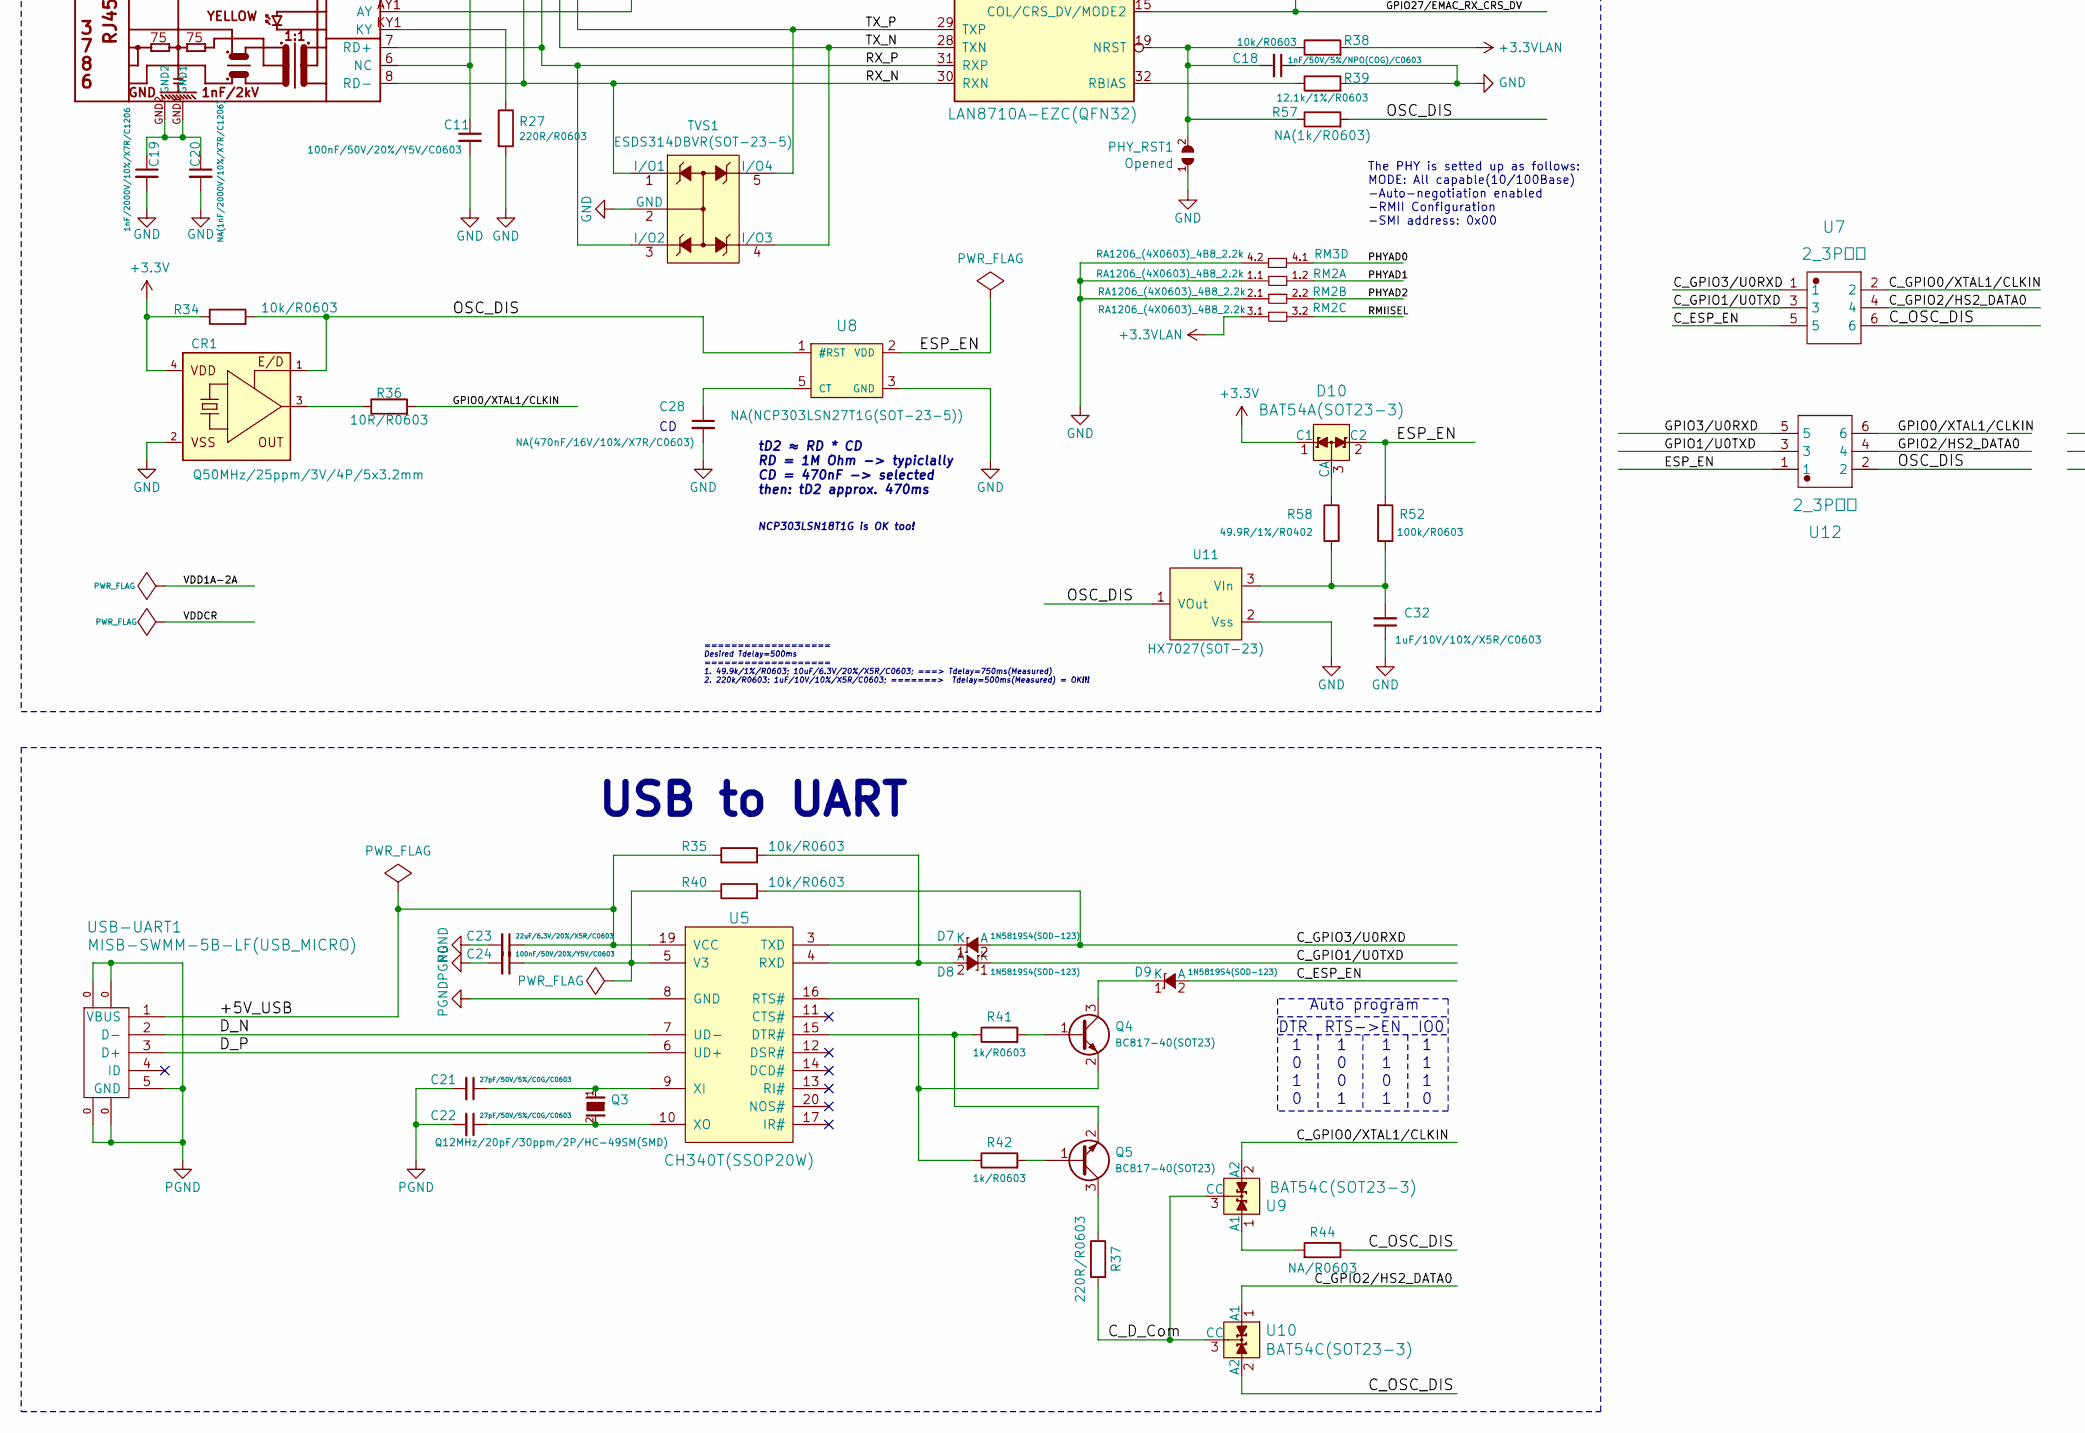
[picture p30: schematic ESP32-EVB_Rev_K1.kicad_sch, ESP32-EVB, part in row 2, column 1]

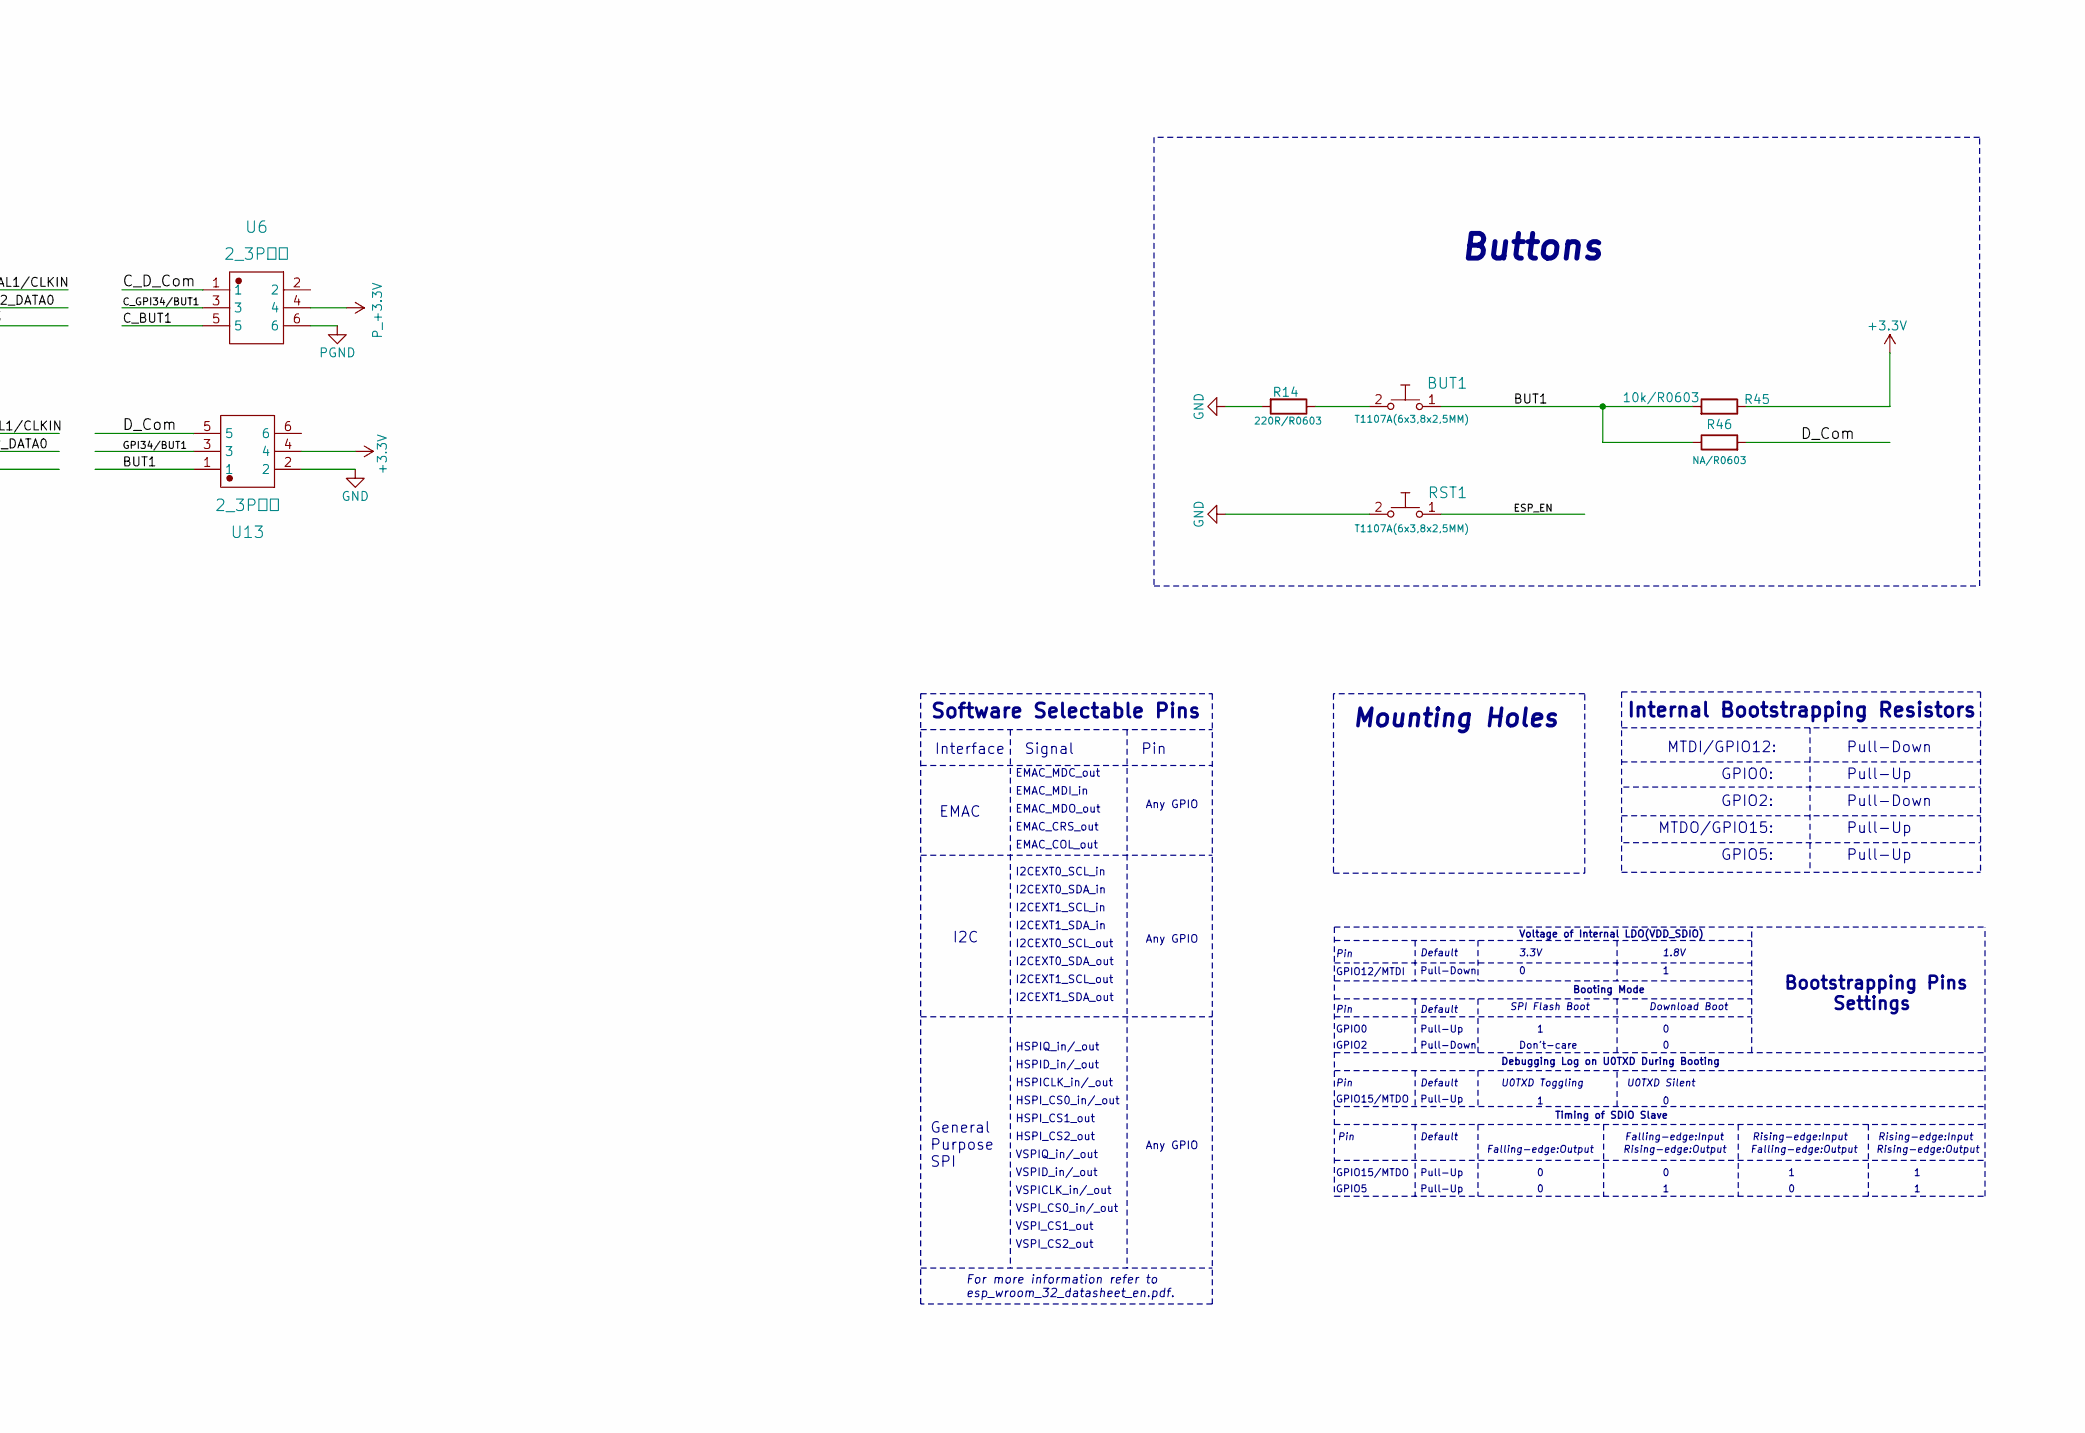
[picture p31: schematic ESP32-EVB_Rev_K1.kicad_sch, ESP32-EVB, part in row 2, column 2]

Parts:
BAT1: DW02R; LIPO_BAT-CON2DW02R
BAT/BUT1: Opened(2-3)/Soldered(1-2); SJ_2_SMALL
BUT1: T1107A(6x3,8x2,5MM)
C1, C3: NA(47uF/6.3V/20%/X5R/C0805); C_0805_5MIL_DWS
C2, C4: 47uF/6.3V/20%/X5R/C0805; C_0805_5MIL_DWS
C6, C7, C8, C9, C12, C23, C29: 22uF/6.3V/20%/X5R/C0603; C_0603_5MIL_DWS
C11, C13, C14, C15, C17, C24, C30: 100nF/50V/20%/Y5V/C0603; C_0603_5MIL_DWS
C16: 2.2uF/6.3V/10%/X5R/C0603; C_0603_5MIL_DWS
C18: 1nF/50V/5%/NPO(COG)/C0603; C_0603_5MIL_DWS
C19: 1nF/2000V/10%/X7R/C1206; C_1206_5MIL_DWS_ISO
C20: NA(1nF/2000V/10%/X7R/C1206); C_1206_5MIL_DWS_ISO
C21, C22: 27pF/50V/5%/C0G/C0603; C_0603_5MIL_DWS
C28: NA(470nF/16V/10%/X7R/C0603); C_0603_5MIL_DWS
C31, C32: 1uF/10V/10%/X5R/C0603; C_0603_5MIL_DWS
CHARGE1: LED/Yellow/0603; LED_0603_KA
CR1: Q50MHz/25ppm/3V/4P/5x3.2mm; 5032-4P_HCX-3S
D2: SMBJ6.0A(DO-214AA); DO214AA_1(K)-2(A)
D4, D6: 1N5822/SS34/SMA; SMA-KA
D7, D8, D9: 1N5819S4(SOD-123); SOD-123_1C-2A_KA
D10: BAT54A(SOT23-3); SOT23-3
FET1, FET2, FET3: WPM2015-3/TR; SOT23
FET4: BSS138; SOT23
L2: 2.2uH/1.5A/DCR=72mR/20%/3.00x3.00x1.50mm/CD32(NR3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; CD32
L3: FB0805/600R/2A; L_0805_5MIL_DWS
L5: NA(FB0805/600R/2A); L_0805_5MIL_DWS
LAN1: RJLD-060TC1(LPJ4013EDNL); RJLBC-060TC1
PHY_RST1: Opened; SJ
PWR1: PWRJ-2mm(YDJ-1134); PWRJ-2mm(YDJ-1136)
PWR2: NA(TB2 DG306-5.0-2P); TB2-DG306-5.0_2P
PWRLED1: LED/RED/0603; LED_0603_KA
Q3: Q12MHz/20pF/30ppm/2P/HC-49SM(SMD); Q_49U3HMS
Q4, Q5: BC817-40(SOT23); SOT23
R4, R7: 2.2k/R0603; R_0603_5MIL_DWS
R8: 2k/1%/R0603; R_0603_5MIL_DWS
R9, R10: 470k/R0603; R_0603_5MIL_DWS
R14, R26, R27, R37: 220R/R0603; R_0603_5MIL_DWS
R17, R44, R46, R54: NA/R0603; R_0603_5MIL_DWS
R19: 220k/R0603; R_0603_5MIL_DWS
R20: 49.9k/1%/R0603; R_0603_5MIL_DWS
R24, R30, R34, R35, R38, R40, R45, R51: 10k/R0603; R_0603_5MIL_DWS
R25: 0R(board_mounted); 0R_0603
R28, R31, R32, R33, R58: 49.9R/1%/R0402; R_0402_5MIL_DWS
R36: 10R/R0603; R_0603_5MIL_DWS
R39: 12.1k/1%/R0603; R_0603_5MIL_DWS
R41, R42, R50: 1k/R0603; R_0603_5MIL_DWS
R52: 100k/R0603; R_0603_5MIL_DWS
R57: NA(1k/R0603); R_0603_5MIL_DWS
RM2, RM3: RA1206_(4X0603)_4B8_2.2k; R_MATRIX_4
RST1: T1107A(6x3,8x2,5MM)
TVS1: ESDS314DBVR(SOT-23-5); SOT-23-5
U1: BL4054B-42TPRN(SOT23-5); SOT-23-5
U2: SY8089AAAC(SOT23-5); SOT-23-5
U3: ESP-WROOM-32; ESP-WROOM-32_MODULE
U4: LAN8710A-EZC(QFN32); QFN32_EP(33)_5.00x5.00x0.90mm_Pitch_0.50mm
U5: CH340T(SSOP20W); SSOP-20W
U6, U7, U12, U13: 2_3P针座; 2.0MM
U8: NA(NCP303LSN27T1G(SOT-23-5)); SOT-23-5
U9, U10: BAT54C(SOT23-3); SOT23-3
U11: HX7027(SOT-23); SOT-23
USB-UART1: MISB-SWMM-5B-LF(USB_MICRO); USB-MICRO_MISB-SWMM-5B_LF

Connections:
+3.3V: C29.1, CR1.4 (VDD), D10.1 (C1), FET3.2, L5.1, R24.1, R34.1, R45.1, R51.1, R54.2, U3.2 (3V3), U13.4
+3.3VLAN: C8.1, C9.1, C13.1, FET3.3, L3.1, L5.2, R38.2, RM2.3.1, RM2.4.1, RM3.1.2, RM3.2.2, RM3.3.2, U4.12 (VDDIO)
+5V: C1.1, C2.1, CHARGE1.2 (A), D2.1 (K), D4.2 (A), D6.1 (K), FET1.1, FET2.2, PWRLED1.2 (A), U1.4 (VCC)
/+5V_EXT: D6.2 (A), FET2.1, PWR1.+, PWR2.1, R30.1
/+5V_USB: C23.1, FET2.3, R35.1, U5.19 (VCC), USB-UART1.1 (VBUS)
/BUT1: BUT1.1, R45.2, R46.1, U13.1
/C_BUT1: BAT/BUT1.1, U6.5
/C_D_Com: R37.2, U6.1, U9.3 (CC), U10.3 (CC)
/C_ESP_EN: D9.2 (A), U7.5
/C_GPI34/BUT1: BAT/BUT1.2, U6.3
/C_GPIO0/XTAL1/CLKIN: U7.2, U9.2 (A2)
/C_GPIO1/U0TXD: D8.1 (K), U7.3
/C_GPIO2/HS2_DATA0: U7.4, U10.1 (A1)
/C_GPIO3/U0RXD: D7.2 (A), R40.2, U7.1
/C_OSC_DIS: R44.1, U7.6, U10.2 (A2)
/D_Com: R46.2, U13.5
/D_N: U5.7 (UD-), USB-UART1.2 (D-)
/D_P: U5.6 (UD+), USB-UART1.3 (D+)
/ESP_EN: C31.2, D10.2 (C2), R24.2, R52.2, RST1.1, U3.3 (EN), U8.2 (VDD), U12.1
/G: LAN1.AG1 (AG), R26.2
/GPI34/BUT1: U3.6 (GPI34/ADC1_CH6/RTC_GPIO4), U13.3
/GPI35/CAN-RX: U3.7 (GPI35/ADC1_CH7/RTC_GPIO5)
/GPI36/U1RXD: U3.4 (GPI36/SENSOR_VP/ADC_H/ADC1_CH0/RTC_GPIO0)
/GPI39/IR_RECEIVE: U3.5 (GPI39/SENSOR_VN/ADC1_CH3/ADC_H/RTC_GPIO3)
/GPIO0/XTAL1/CLKIN: R36.2, R54.1, U3.25 (GPIO0/ADC2_CH1/TOUCH1/RTC_GPIO11/CLK_OU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), U4.5 (XTAL1/CLKIN), U12.6
/GPIO1/U0TXD: U3.35 (GPIO1/U0TXD/CLK_OUT3/EMAC_RXD2), U12.3
/GPIO2/HS2_DATA0: U3.24 (GPIO2/ADC2_CH2/TOUCH2/RTC_GPIO12/HSPIWP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), U12.4
/GPIO3/U0RXD: U3.34 (GPIO3/U0RXD/CLK_OUT2), U12.5
/GPIO4/U1TXD: U3.26 (GPIO4/ADC2_CH0/TOUCH0/RTC_GPIO10/HSPIHD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)
/GPIO5/CAN-TX: U3.29 (GPIO5/VSPICS0/HS1_DATA6/EMAC_RX_CLK)
/GPIO6/SD_CLK: U3.20 (GPIO6/SD_CLK/SPICLK/HS1_CLK/U1CTS)
/GPIO7/SD_DATA0: U3.21 (GPIO7/SD_DATA0/SPIQ/HS1_DATA0/U2RTS)
/GPIO8/SD_DATA1: U3.22 (GPIO8/SD_DATA1/SPID/HS1_DATA1/U2CTS)
/GPIO9/SD_DATA2: U3.17 (GPIO9/SD_DATA2/SPIHD/HS1_DATA2/U1RXD)
/GPIO10/SD_DATA3: U3.18 (GPIO10/SD_DATA3/SPIWP/HS1_DATA3/U1TXD)
/GPIO11/SD_CMD: U3.19 (GPIO11/SD_CMD/SPICS0/HS1_CMD/U1RTS)
/GPIO12/IR_Transmit: U3.14 (GPIO12/ADC2_CH5/TOUCH5/RTC_GPIO15/MTDI/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)
/GPIO13/I2C-SDA: U3.16 (GPIO13/ADC2_CH4/TOUCH4/RTC_GPIO14/MTCK/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)
/GPIO14/HS2_CLK: U3.13 (GPIO14/ADC2_CH6/TOUCH6/RTC_GPIO16/MTMS/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)
/GPIO15/HS2_CMD: U3.23 (GPIO15/ADC2_CH3/TOUCH3/MTDO/HSPICS0/RTC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)
/GPIO16/I2C-SCL: U3.27 (GPIO16/HS1_DATA4/U2RXD/EMAC_CLK_OUT)
/GPIO17/SPI_CS: U3.28 (GPIO17/HS1_DATA5/U2TXD/EMAC_CLK_OUT_180)
/GPIO18/MDIO(RMII): RM3.1.1, U3.30 (GPIO18/VSPICLK/HS1_DATA7), U4.16 (MDIO)
/GPIO19/EMAC_TXD0(RMII): U3.31 (GPIO19/VSPIQ/U0CTS/EMAC_TXD0), U4.22 (TXD0)
/GPIO21/EMAC_TX_EN(RMII): U3.33 (GPIO21/VSPIHD/EMAC_TX_EN), U4.21 (TXEN)
/GPIO22/EMAC_TXD1(RMII): U3.36 (GPIO22/VSPIWP/U0RTS/EMAC_TXD1), U4.23 (TXD1)
/GPIO23/MDC(RMII): U3.37 (GPIO23/VSPID/HS1_STROBE), U4.17 (MDC)
/GPIO25/EMAC_RXD0(RMII): RM3.3.1, U3.10 (GPIO25/DAC_1/ADC2_CH8/RTC_GPIO6/EMAC_RX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), U4.11 (RXD0/MODE0)
/GPIO26/EMAC_RXD1(RMII): RM2.4.2, U3.11 (GPIO26/DAC_2/ADC2_CH9/RTC_GPIO7/EMAC_RX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), U4.10 (RXD1/MODE1)
/GPIO27/EMAC_RX_CRS_DV: RM3.2.1, U3.12 (GPIO27/ADC2_CH7/TOUCH7/RTC_GPIO17/EMAC_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), U4.15 (COL/CRS_DV/MODE2)
/GPIO32/REL1: U3.8 (GPIO32/XTAL_32K_P/ADC1_CH4/TOUCH9/RTC_G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)
/GPIO33/REL2: U3.9 (GPIO33/XTAL_32K_N/ADC1_CH5/TOUCH8/RTC_G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)
/OSC_DIS: CR1.1 (E/D), FET4.1 (G), R34.2, R57.2, U8.1 (#RST), U11.1 (VOut), U12.2
/PHYAD0: RM3.4.1, U4.13 (RXER/RXD4/PHYAD0)
/PHYAD1: RM2.1.2, U4.7 (RXCLK/PHYAD1)
/PHYAD2: RM2.2.2, U4.8 (RXD3/PHYAD2)
/RMIISEL: RM2.3.2, U4.9 (RXD2/RMIISEL)
/RX_N: LAN1.8 (RD-), R28.2, TVS1.1 (I/O1), U4.30 (RXN)
/RX_P: LAN1.7 (RD+), R31.2, TVS1.3 (I/O2), U4.31 (RXP)
/TX_N: LAN1.2 (TD-), R32.2, TVS1.4 (I/O3), U4.28 (TXN)
/TX_P: LAN1.1 (TD+), R33.2, TVS1.5 (I/O4), U4.29 (TXP)
/VDD1A-2A: C12.1, C14.1, C15.1, L3.2, R25.1, R26.1, R28.1, R31.1, R32.1, R33.1, U4.1 (VDD2A), U4.27 (VDD1A)
/VDDCR: C16.1, C17.1, U4.6 (VDDCR)
GND: C8.2, C9.2, C11.2, C12.2, C13.2, C14.2, C15.2, C16.2, C17.2, C18.1, C19.2, C20.2, C28.2, C31.1, C32.1, CR1.2 (VSS), FET4.2 (S), PHY_RST1.1, R14.2, R27.2, R39.2, RM2.1.1, RM2.2.1, RM3.4.2, RST1.2, TVS1.2 (GND), U3.1 (GND), U3.15 (GND), U3.38 (GND), U3.39 (THERMAL_PAD), U4.24 (TXD2), U4.25 (TXD3), U4.33 (GND), U8.3 (GND), U11.2 (Vss), U13.2
unnamed: BAT/BUT1.3, C30.1, R9.2, R10.1
unnamed: BUT1.2, R14.1
unnamed: C19.1, C20.1, LAN1.GND1, LAN1.GND2
unnamed: C29.2, FET3.1, R50.2, R51.2
unnamed: CHARGE1.1 (K), R7.2
unnamed: CR1.3 (OUT), R36.1
unnamed: C3.1, C4.1, D4.1 (K), FET1.2, R17.2, U2.1 (EN), U2.4 (IN)
unnamed: D7.1 (K), U5.3 (TXD)
unnamed: D8.2 (A), R35.2, U5.4 (RXD)
unnamed: D9.1 (K), Q4.3 (C)
unnamed: D10.3 (CA), R58.1
unnamed: FET4.3 (D), R50.1
unnamed: LAN1.AY1 (AY), U4.3 (LED1/REGOFF)
unnamed: C11.1, LAN1.3 (COM), LAN1.6 (NC), R25.2
unnamed: LAN1.KG1 (KG), U4.2 (LED2/NINTSEL)
unnamed: LAN1.KY1 (KY), R27.1
unnamed: PWRLED1.1 (K), R4.1
unnamed: Q4.1 (B), R41.2
unnamed: Q4.2 (E), R42.1, U5.16 (RTS#)
unnamed: Q5.1 (B), R42.2
unnamed: Q5.3 (C), R37.1
unnamed: Q5.2 (E), R41.1, U5.15 (DTR#)
unnamed: R7.1, U1.1 (CHRGb)
unnamed: R8.2, U1.5 (PROG)
unnamed: BAT1.1, FET1.3, R9.1, R17.1, U1.3 (VBAT)
unnamed: R19.1, R20.1, U2.5 (FB)
unnamed: L2.1, U2.3 (LX)
unnamed: C18.2, PHY_RST1.2, R38.1, R57.1, U4.19 (NRST)
unnamed: R39.1, U4.32 (RBIAS)
unnamed: C24.1, R40.1, U5.5 (V3)
unnamed: C21.1, Q3.1, U5.9 (XI)
unnamed: C22.1, Q3.2, U5.10 (XO)
unnamed: C28.1, U8.5 (CT)
unnamed: R44.2, U9.1 (A1)
unnamed: C32.2, R52.1, R58.2, U11.3 (VIn)
PGND: BAT1.2, C1.2, C2.2, C3.2, C4.2, C6.2, C7.2, C21.2, C22.2, C23.2, C24.2, C30.2, D2.2 (A), PWR1.-, PWR2.2, R4.2, R8.1, R10.2, R20.2, R30.2, U1.2 (GND), U2.2 (GND), U5.8 (GND), U6.6, USB-UART1.0, USB-UART1.5 (GND)
P_+3.3V: C6.1, C7.1, L2.2, R19.2, U6.4

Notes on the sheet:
Software Selectable Pins
Timing of SDIO Slave
GPIO0
I2CEXT1_SDA_out
GPIO15/MTDO
Pull-Down
GPIO0:
Debugging Log on U0TXD During Booting
For more information refer to esp_wroom_32_datasheet_en.pdf.
GPIO2
Pin
EMAC
Default
Pull-Up
I2CEXT0_SDA_out
VSPI_CS2_out
I2C
Rising-edge:Input
Battery Measurement
Falling-edge:Output
USB to UART
IBAT = 1000/Rprog = 500mA
VSPID_in/_out
Signal
HSPI_CS2_out
GPIO5:
Power Supply
HSPID_in/_out
I2CEXT1_SCL_in
Rprog
I2CEXT0_SCL_in
Auto program
Internal Bootstrapping Resistors
EMAC_MDC_out
Ethernet
I2CEXT1_SDA_in
DTR RTS->EN IO0
The PHY is setted up as follows: MODE: All capable(10/100Base) -Auto-negotiation enabled -RMII Configuration -SMI address: 0x00
LiPo Charger
EMAC_MDO_out

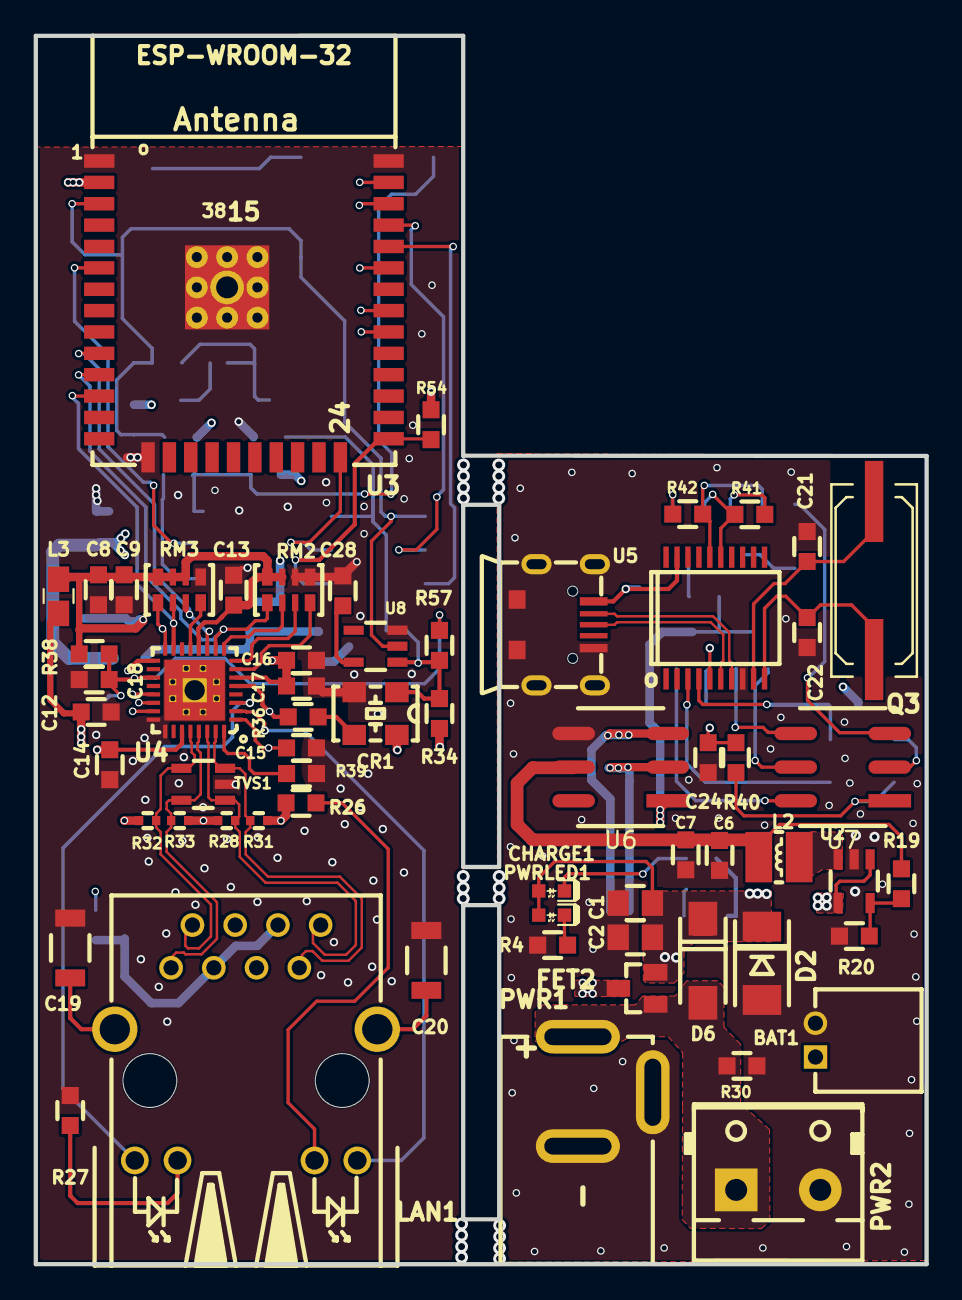
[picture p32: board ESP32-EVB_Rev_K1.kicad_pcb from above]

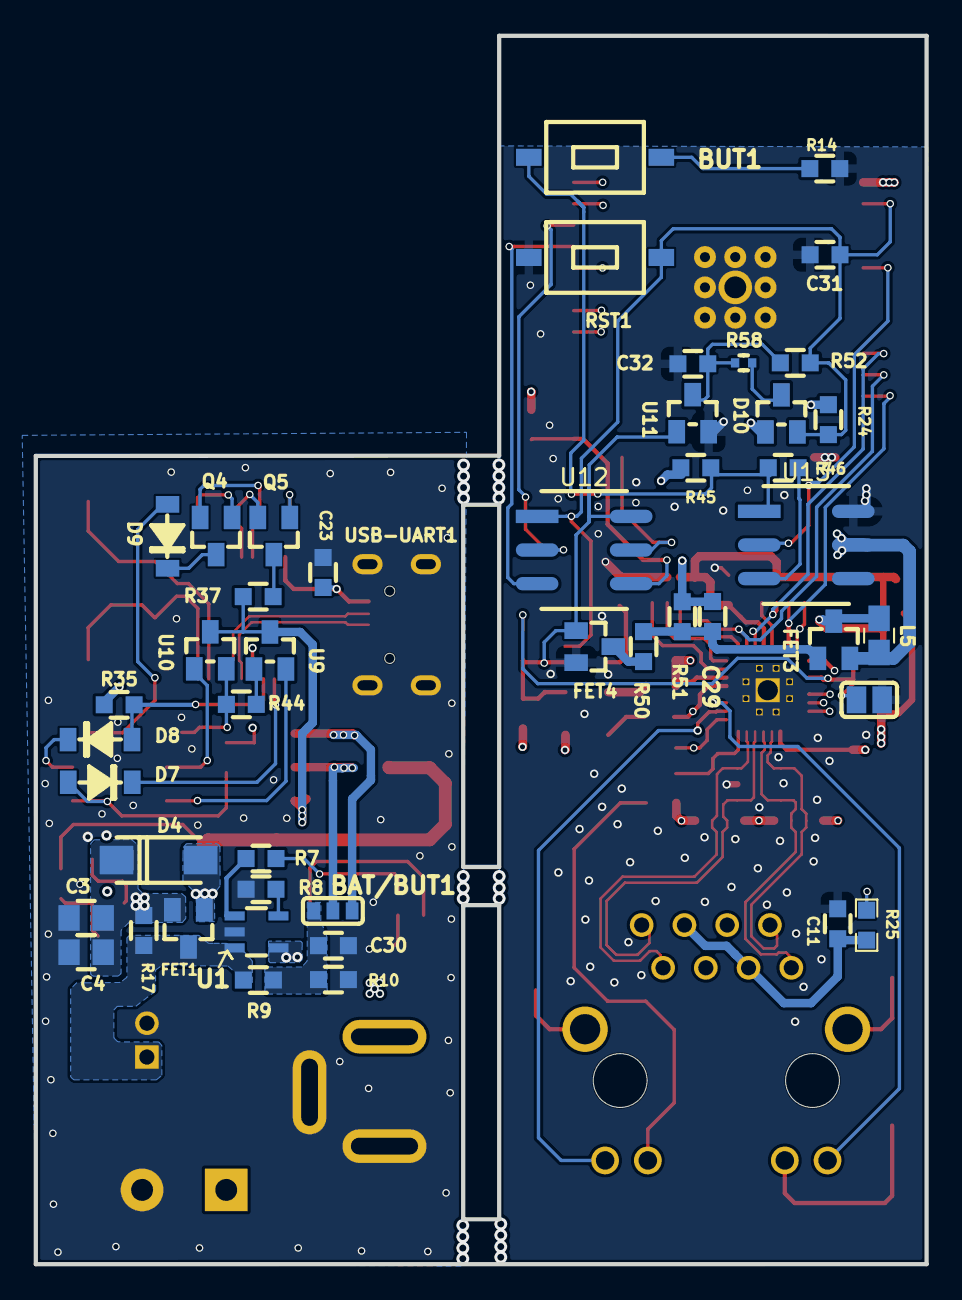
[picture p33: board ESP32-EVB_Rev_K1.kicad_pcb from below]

Board: 4 copper layers, 52.9 x 73.0 mm, 108 parts (46 on the bottom side), 82 nets.

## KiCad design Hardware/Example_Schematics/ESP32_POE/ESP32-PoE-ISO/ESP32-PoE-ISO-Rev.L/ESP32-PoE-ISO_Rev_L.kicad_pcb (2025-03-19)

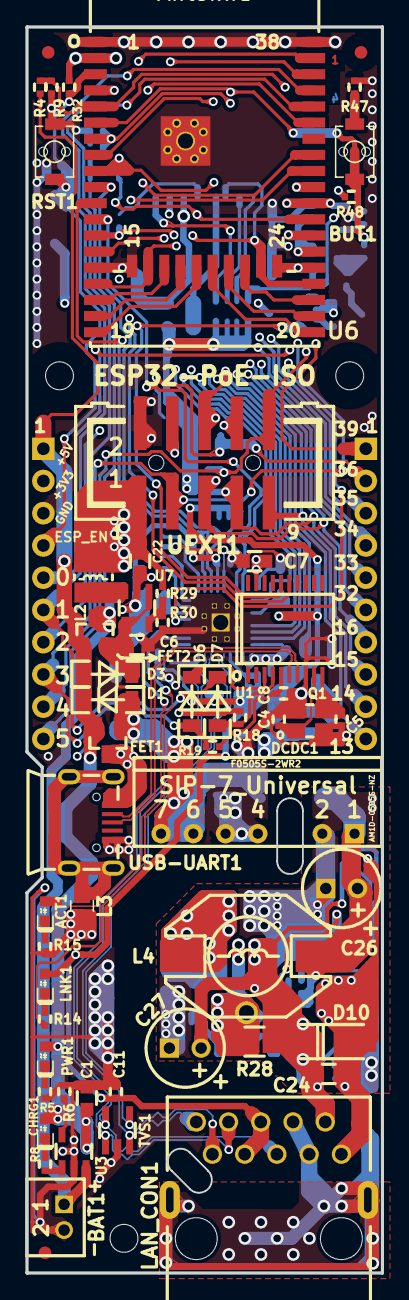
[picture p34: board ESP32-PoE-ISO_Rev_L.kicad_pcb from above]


Board: 4 copper layers, 28.0 x 98.2 mm, 145 parts (84 on the bottom side), 97 nets.

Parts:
ACT1: LED/YELLOW/0603; LED_0603_KA
BAT1: DW02S; LIPO_BAT_VERTICAL_DW02S
BUT1: IT1185AU2; IT1185AU2_V2
C1, C6, C7, C9, C10, C13, C19, C22: 22uF/6.3V/20%/X5R/C0603; C_0603_5MIL_DWS
C2: 1nF/2000V/10%/X7R/C1206; C_1206_5MIL_DWS_ISO
C3: 47uF/6.3V/20%/X5R/C0805; C_0805_5MIL_DWS
C4, C5: 27pF/50V/5%/C0G/C0402; C_0402_5MIL_DWS
C8, C11, C14, C15, C16, C18, C29: 100nF/16V/10%/X7R/C0402; C_0402_5MIL_DWS
C12, C24: 100nF/100V/10%/X7R/C0603; C_0603_5MIL_DWS
C17: 2.2uF/6.3V/10%/X5R/C0603; C_0603_5MIL_DWS
C20: NA(1.0nF/3kV/10%/X7R/SMD/1808(VISHAY-VJ1808Y102KB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; C_1808(4520)_5MIL_DWS_ISO
C21: NA(10uF/6.3V/20%/X5R/C0603); C_0603_5MIL_DWS
C23: 1.0nF/3kV/10%/X7R/SMD/1808(VISHAY-VJ1808Y102KBHAT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; C_1808(4520)_5MIL_DWS_ISO
C25: 12pF/50V/5%/COG/C0402; C_0402_5MIL_DWS
C26: 470uF/10V/20%/Low_ESR/RM2.5/6.0x11mm; CPOL-RM2.5mm_6.3x11mm_PTH
C27: 15uF/100V/20%/RM2.5/6.3x11mm(Farnell:1281844); CPOL-RM2.5mm_6.3x11mm_PTH
C28: 1nF/50V/10%/X7R/C0402; C_0402_5MIL_DWS
C31: 1uF/10V/20%/X5R/C0603; C_0603_5MIL_DWS
CHRG1: LED/YELLOW/0603; LED_0603_KA
D1, D3, D4, D6, D7, D9: 1N5819S4/SOD123; SOD-123_1C-2A_KA
D2: BAT54C(SOT23-3); SOT23-3
D5: SS510/100V/5A/0.85V/DO214AB(SMC); DO214AB(SMC)_1(K)-2(A)
D8: NA(SMBJ6.0A); DO214AA_1(K)-2(A)
D10: SMAJ58A/SMA; SMA-KA
DCDC1: F0505S-2WR2(SIP-7); SIP-7_Universal
Drill_Slot1, Drill_Slot3: 2 mm; Mounting_hole_2_mm
EXT1, EXT2: NS(HN1x10); HN1x10
FET1, FET2, FET3: WPM2015-3/TR; SOT23
FID1, FID2, FID3, FID4, FID5, FID6: Fiducial; Fiducial1x3
L1, L3, L5: FB0805/600R/2A; L_0805_5MIL_DWS
L2: 2.2uH/1.5A/DCR=72mR/20%/3.00x3.00x1.50mm/CD32(NR3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; CD32
L4: 33uH/2.1A/DCR=0.1R/20%/DBS135(PD3316MT330); DBS135
LAN_CON1: RJP-003TC1(LPJ4112CNL)
LNK1: LED/GREEN/0603; LED_0603_KA
Logo_OSHW: LOGO_OPENHARDWARE_8x8
Logo_Olimex: OLIMEX_LOGO_TB
MH1, MH2, MH3: Mounting_Hole_NPTH; NPTH_2.2mm
MICRO_SD1: TFC-9P-1.7H(ATFFS150A01BR016); uSD(TFC-9P-1.xH(ATFFS150A01BR016))
PWR1: LED/RED/0603; LED_0603_KA
Q1: Q12MHz/20pF/10ppm/4P/3.2x2.5mm; TSX-3.2x2.5mm_GND(3)
Q2, Q3: BC817-40(SOT23); SOT23
R1, R2, R6, R18, R19, R25, R32, R36, R37, R39, R44, R48: 10k/R0402; R_0402_5MIL_DWS
R3, R20, R21: 1k/R0402; R_0402_5MIL_DWS
R4: 47k/R0402; R_0402_5MIL_DWS
R5, R8, R14, R15, R31, R35: 2.2k/R0402; R_0402_5MIL_DWS
R7, R16: 470k/R0402; R_0402_5MIL_DWS
R9: 100k/R0402; R_0402_5MIL_DWS
R10, R11, R12, R13: 49.9R/1%/R0402; R_0402_5MIL_DWS
R17, R49: NA/R0402; R_0402_5MIL_DWS
R22: 24.9k/1%/R0402; R_0402_5MIL_DWS
R23: 180k/1%/R0402; R_0402_5MIL_DWS
R24, R46, R47: 220R/R0402; R_0402_5MIL_DWS
R26: 12.1k/1%/R0402; R_0402_5MIL_DWS
R27: 4.42k/1%/1/16W/R0402; R_0402_5MIL_DWS
R28: 0.03R/1%/R1206; R_1206_5MIL_DWS
R29: 220k/R0402; R_0402_5MIL_DWS
R30: 49.9k/1%/R0402; R_0402_5MIL_DWS
R33: 4.7R/R0402; R_0402_5MIL_DWS
R34: 10.5k/1%/R0402; R_0402_5MIL_DWS
R38: 56.2k/1%/R0402; R_0402_5MIL_DWS
R40, R42: 10R/R0402; R_0402_5MIL_DWS
R41: 4.7k/R2512; R_2512_MM_DWS
R43: 130k/R0402; R_0402_5MIL_DWS
RM1, RM2, RM3: RA1206_(4X0603)_4B8_2.2k; R_MATRIX_4
RST1: IT1185AU2; IT1185AU2_V2
Sign_Antistatic: Val**; LOGO_ANTISTATIC_1
Sign_CE: CE_Sign
Sign_PB-Free: LOGO_PBFREE
Sign_RecycleBin: LOGO_RECYCLEBIN_1
T1: LMUN2211LT1G(SOT-23); SOT23
TVS1: ESDS314DBVR(SOT-23-5); SOT-23-5
TVS2, TVS3: NA(GG0402052R542P); D_0402_5MIL_DWS
U1: CH340T(SSOP20W); SSOP-20W
U2: TPS2376D(SO-8); SOIC-8_1.75mm
U3: BL4054B-42TPRN(SOT23-5); SOT-23-5
U4: LAN8710A-EZC(QFN32); QFN32_EP(33)_5.00x5.00x0.90mm_Pitch_0.50mm
U5: TX4138(ESOIC-8); ESOIC-8
U6: ESP32-WROVER-E; ESP32-WROVER(WROOM)-UNIVERSAL_MODULE
U7: SY8089AAAC(SOT23-5); SOT-23-5
U8: SN74LVC1G04DBVR(SOT23-5); SOT-23-5
UEXT1: P-B-V-10-LF; GBH-254-SMT-10
USB-UART1: MISB-SWMM-5B-LF(USB_MICRO); USB-MICRO_MISB-SWMM-5B_LF

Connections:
+3.3VLAN: C9.1, C14.1, C29.2, FET3.3, L1.1, R25.2, RM1.4.1, RM2.1.1, RM2.2.1, RM2.3.1, RM2.4.1, U4.12, U8.5
+3V3: C10.1, C22.1, EXT1.2, FET3.2, L2.2, L5.1, R2.1, R17.1, R29.2, R31.1, R32.1, R35.1, R36.1, R37.1, R39.1, R48.1, RM3.1.2, RM3.2.2, RM3.3.2, RM3.4.2, U6.2, UEXT1.1
+5V: C1.1, CHRG1.2, D1.1, D3.2, EXT1.1, FET1.2, FET2.1, PWR1.2, R4.1, U3.4
+5VP: C19.1, C20.1, D1.2, D8.1, DCDC1.6, DCDC1.7, FET1.1, R1.1
/5V_DCDC: C20.2, C25.1, C26.1, DCDC1.1, L4.2, R38.1
/+5V_USB: C7.1, FET1.3, R18.1, U1.19, USB-UART1.1
/D_Com: D2.3, R24.2, R49.2
/ESP_EN: C31.1, D9.2, EXT1.4, R32.2, RST1.1, U6.3
/GPI34/BUT1: BUT1.1, EXT2.4, R48.2, R49.1, U6.6
/GPI35: C28.1, EXT2.3, R7.2, R16.1, U6.7
/GPI36/U1RXD: D4.2, EXT2.2, R37.2, U6.4
/GPI39: EXT2.1, R4.2, R9.1, U6.5
/GPIO0: D2.2, EXT1.5, U6.25, U8.2
/GPIO1/U0TXD: D7.1, EXT1.6, U6.35
/GPIO2/HS2_DATA0: D2.1, EXT1.7, R46.1, RM3.4.1, U6.24, UEXT1.8
/GPIO3/U0RXD: D6.2, EXT1.8, R17.2, R19.2, U6.34
/GPIO4/U1TXD: EXT1.9, U6.26, UEXT1.3
/GPIO5/SPI_CS: EXT1.10, R36.2, U6.29, UEXT1.10
/GPIO12/PHY_PWR: T1.1, U6.14
/GPIO13/I2C-SDA: EXT2.10, R35.2, U6.16, UEXT1.6
/GPIO14/HS2_CLK: EXT2.9, R40.1, U6.13, UEXT1.9
/GPIO15/HS2_CMD: EXT2.8, MICRO_SD1.3, R39.2, U6.23, UEXT1.7
/GPIO16/I2C-SCL: EXT2.7, R31.2, R42.2, U6.27, UEXT1.5
/GPIO17/EMAC_CLK_OUT_180: U4.5, U6.28, U8.4
/GPIO18/MDIO(RMII): RM2.4.2, U4.16, U6.30
/GPIO19/EMAC_TXD0(RMII): U4.22, U6.31
/GPIO21/EMAC_TX_EN(RMII): U4.21, U6.33
/GPIO22/EMAC_TXD1(RMII): U4.23, U6.36
/GPIO23/MDC(RMII): U4.17, U6.37
/GPIO25/EMAC_RXD0(RMII): RM2.2.2, U4.11, U6.10
/GPIO26/EMAC_RXD1(RMII): RM2.1.2, U4.10, U6.11
/GPIO27/EMAC_RX_CRS_DV: RM2.3.2, U4.15, U6.12
/GPIO32: EXT2.6, U6.8
/GPIO33: EXT2.5, R42.1, U6.9
/ILIM: R28.1, U5.2, U5.9
/RD+: LAN_CON1.3, R11.2, TVS1.1, TVS3.2, U4.31
/RD-: LAN_CON1.6, R10.2, TVS1.5, TVS3.1, U4.30
/Shield: C2.2, LAN_CON1.0, LAN_CON1.7, LAN_CON1.8
/TD+: LAN_CON1.1, R13.2, TVS1.3, TVS2.2, U4.29
/TD-: LAN_CON1.2, R12.2, TVS1.4, TVS2.1, U4.28
/USB_D+: U1.6, USB-UART1.3
/USB_D-: U1.7, USB-UART1.2
Earth: C2.1, C23.2, C26.2, C27.2, D5.2, DCDC1.2, R34.2, R41.2, U2.5, U5.4
GND: BAT1.2, C1.2, C3.2, C4.2, C5.2, C6.2, C7.2, C8.2, C9.2, C11.2, C13.2, C14.2, C15.2, C16.2, C17.2, C18.2, C19.2, C21.1, C22.2, C23.1, C28.2, C29.1, C31.2, D8.2, DCDC1.4, DCDC1.5, EXT1.3, L3.2, MICRO_SD1.6, MICRO_SD1.CH1, Q1.3, R1.2, R5.2, R6.2, R9.2, R15.2, R16.2, R26.2, R30.2, R47.2, RM1.1.1, RM1.2.1, RM1.3.1, RST1.2, T1.2, TVS1.2, U1.8, U3.2, U4.24, U4.25, U4.33, U6.1, U6.15, U6.38, U6.39, U7.2, U8.3, UEXT1.2, USB-UART1.5
unnamed: ACT1.1, R15.1
unnamed: ACT1.2, U4.3
unnamed: BAT1.1, FET2.3, R7.1, U3.3
unnamed: BUT1.2, R47.1
unnamed: C3.1, L5.2, MICRO_SD1.4
unnamed: C4.1, Q1.1, U1.9
unnamed: C5.1, Q1.2, U1.10
unnamed: C6.1, D3.1, FET2.2, U7.1, U7.4
unnamed: C8.1, R19.1, U1.5
unnamed: C10.2, FET3.1, R2.2, R3.1
unnamed: C11.1, C13.1, C15.1, C16.1, L1.2, LAN_CON1.4, LAN_CON1.5, LNK1.2, R10.1, R11.1, R12.1, R13.1, U4.1, U4.27
unnamed: C12.1, D5.1, L4.1, U5.1
unnamed: C12.2, R33.2
unnamed: C17.1, C18.1, U4.6
unnamed: C21.2, R25.1, U4.19
unnamed: C25.2, R34.1, R38.2, U5.5
unnamed: CHRG1.1, R8.1
unnamed: D4.1, UEXT1.4
unnamed: D6.1, U1.3
unnamed: D7.2, R18.2, U1.4
unnamed: D9.1, Q2.3
unnamed: L2.1, U7.3
unnamed: L3.1, USB-UART1.0
unnamed: LNK1.1, R14.1
unnamed: MICRO_SD1.1, RM3.3.1
unnamed: MICRO_SD1.2, RM3.2.1
unnamed: MICRO_SD1.5, R40.2
unnamed: MICRO_SD1.7, R46.2
unnamed: MICRO_SD1.8, RM3.1.1
unnamed: PWR1.1, R5.1
unnamed: Q2.1, R20.2
unnamed: Q2.2, R21.1, U1.16
unnamed: Q3.1, R21.2
unnamed: Q3.2, R20.1, U1.15
unnamed: Q3.3, R24.1
unnamed: R3.2, T1.3
unnamed: R6.1, U3.5
unnamed: R8.2, U3.1
unnamed: R14.2, U4.2
unnamed: R22.2, U2.3
unnamed: R23.1, U2.1
unnamed: R26.1, U4.32
unnamed: R27.2, U2.2
unnamed: R29.1, R30.1, U7.5
unnamed: R33.1, U5.8
unnamed: R43.2, R44.1, U2.7
unnamed: RM1.1.2, U4.7
unnamed: RM1.2.2, U4.8
unnamed: RM1.3.2, U4.13
unnamed: RM1.4.2, U4.9
unnamed: U2.6, U5.6
Spare1: C24.1, C27.1, D10.1, LAN_CON1.9, R22.1, R28.2, R41.1, R43.1, U2.8, U5.3
Spare2: C24.2, D10.2, LAN_CON1.10, R23.2, R27.1, R44.2, U2.4

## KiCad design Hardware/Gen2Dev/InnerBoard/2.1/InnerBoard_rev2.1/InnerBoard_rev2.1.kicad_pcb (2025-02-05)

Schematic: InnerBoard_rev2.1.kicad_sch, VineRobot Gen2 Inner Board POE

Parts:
C1: 15uF; C_0805_2012Metric; Mfr P/N CL10A106KP8NNNC
C2, C8: 100pF; C_0805_2012Metric; Mfr P/N CL10A106KP8NNNC
C3: 220nF; C_0805_2012Metric; Mfr P/N CL10A106KP8NNNC
C4: 470pF; C_0805_2012Metric; Mfr P/N CL10A106KP8NNNC
C5: 12nF; C_0805_2012Metric; Mfr P/N CL10A106KP8NNNC
C6, C61, C62, C64, C65, C68, C70: 100nF; C_0805_2012Metric; Mfr P/N CL10A106KP8NNNC
C7, C72: 1uF; C_0805_2012Metric; Mfr P/N CL10A106KP8NNNC
C20, C22, C31: 10uF; C_0805_2012Metric; Mfr P/N CL10A106KP8NNNC
C21, C23: 1uF; C_0805_2012Metric; Mfr P/N CC0201MRX5R6BB105
C24, C29: 18pF; C_0402_1005Metric; Mfr P/N CL10A106KP8NNNC
C25, C26: 100nF; C_0805_2012Metric
C27: 10uF; C_0805_2012Metric
C32: 1uF; C_0805_2012Metric
C59, C69: 1nF; C_0805_2012Metric; Mfr P/N CL10A106KP8NNNC
C60, C66, C67, C71: 22uF; C_0805_2012Metric; Mfr P/N CL10A106KP8NNNC
C63: 2.2uF; C_0805_2012Metric; Mfr P/N CL10A106KP8NNNC
D4, D5, D7, D11: LED; LED_0603_1608Metric; Mfr P/N 19-21/GHC-YR1S2/4T
D6: 1N5819; D_DO-41_SOD81_P10.16mm_Horizontal
D10, D13, D14: 1N5819WS; D_SOD-323
D15: BAT54C; SOT-23
D23: SMAJ58A; D_SMA
D24: BAT54A; SOT-23
FID1, FID2, FID3, FID4: Fiducial; Fiducial_0.5mm_Mask1.5mm
H1, H2, H3, H4: MountingHole; MountingHole_2.1mm
J1, J2, J3, J4, J7, J9, J10, J11, J12, J13, J14, J15, J16, J17, J18, J19: HMTSW-102-X-X-S-X; SAMTEC_HMTSW-102-X-X-S-X; PARTREV A
J5: UJ31-CH-G2-SMT-TR; CUI_UJ31-CH-G2-SMT-TR; PART_REV 1.01
J8: 3221-10-0300-00; CONN10_3221-10-0300-00_CNC; Mfr P/N 3221-10-0300-00
J25: SI-46020-F; BEL_SI-46020-F; PARTREV C
JP1: SolderJumper_2_Open; SolderJumper-2_P1.3mm_Open_Pad1.0x1.5mm
L8, L9: 600R/2A; L_0805_2012Metric
MH2, MH3: Mounting_hole_Shield_3.3mm; MountingHole_3.2mm_M3_Pad_Via; not fitted
Q1, Q9: SI2323DS-T1-GE3; SOT23
Q4, Q5: BC817; SOT-23
Q10: BSS138; SOT-23
R1: 130k; R_0805_2012Metric; Mfr P/N AC0201FR-07100RL
R2, R21, R30, R97, R100, R101: 10k; R_0805_2012Metric; Mfr P/N AC0201FR-07100RL
R3: 18k; R_0805_2012Metric; Mfr P/N AC0201FR-07100RL
R4: 8.25k; R_0805_2012Metric; Mfr P/N AC0201FR-07100RL
R5: 9.3k; R_0805_2012Metric; Mfr P/N AC0201FR-07100RL
R6: 6k; R_0805_2012Metric; Mfr P/N AC0201FR-07100RL
R7, R23, R25, R28, R51: 100; R_0805_2012Metric; Mfr P/N AC0201FR-07100RL
R8: 5.24M; R_0805_2012Metric; Mfr P/N AC0201FR-07100RL
R22, R29, R104, R105, R106, R107: 2.2k; R_0805_2012Metric; Mfr P/N AC0201FR-07100RL
R24: 0; R_0805_2012Metric; not fitted
R26, R42, R47, R52: 10k; R_0805_2012Metric
R27: 5.1K; R_0805_2012Metric; Mfr P/N RC0201FR-075K1L
R31: 12.1k; R_0805_2012Metric; Mfr P/N AC0201FR-07100RL
R32, R99: 1k; R_0805_2012Metric; Mfr P/N AC0201FR-07100RL
R33, R81, R82, R83: 49.9; R_0805_2012Metric; Mfr P/N AC0201FR-07100RL
R34, R43: 2.2k; R_0805_2012Metric
R35: 10; R_0805_2012Metric
R41, R45: 1k; R_0805_2012Metric
R46, R49: 220; R_0805_2012Metric
R50: 5.1K; R_0805_2012Metric; Mfr P/N RC0201DR-076K04L
R84, R89: 220; R_0805_2012Metric; Mfr P/N AC0201FR-07100RL
R90: 24.9k; R_0805_2012Metric; Mfr P/N AC0201FR-07100RL
R93: 180k; R_0805_2012Metric; Mfr P/N AC0201FR-07100RL
R94: 4.42k; R_0805_2012Metric; Mfr P/N AC0201FR-07100RL
R108: 49.9k; R_0805_2012Metric; Mfr P/N AC0201FR-07100RL
R109: 100k; R_0805_2012Metric; Mfr P/N AC0201FR-07100RL
SW1: PTS815 SJM 250 SMTR LFS; SW4_PTS815 SJM 250 SMTR LFS_CNK; Mfr P/N PTS815SJG250SMTRLFS
TP1, TP2, TP3, TP4, TP5, TP6, TP8, TP9, TP10, TP11, TP12, TP13, TP14, TP15, TP16, TP18, TP19, TP20, TP21, TP22, TP23, TP24, TP25, TP26, TP27, TP28, TP29, TP30: TestPoint; TestPoint_Pad_D2.0mm
U1: LM5156DSSR; DSS0012B
U4: MIC5504-3.3YM5; SOT-23-5; Mfr P/N MIC5504-3.3YM5-TR
U6: 74LVC1G04; SOT-23-5
U7: LD1117S50TR_SOT223; SOT-223-3_TabPin2
U9: FT232RQ; QFN50P500X500X90-33N; Mfr P/N FT232RQ-REEL
U10: ESP32-WROOM-32E-N8; ESP32­WROOM­32E_EXP
U11: LAN8710A-EZC; QFN32_5X5MC_MCH
U12: TPS2376PW; PW8
U23: ESDS314DBVR; DBV0005A_N
U25: MCP100-270D; TO127P254X495-3
Y1: ABLS2-12.000MHZ-D4Y-T; XTAL_ABLS2-12.000MHZ-D4Y-T; PARTREV 11.15.2016
Y3: ASV-50.000MHZ-LCS-T; XTAL_ASV-50.000MHZ-LCS-T; PARTREV 09.02.14

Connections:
+3.3V: C22.1, C23.1, C31.1, C71.1, D24.1, J4.01, J8.10, J9.02, L9.1, Q9.2, R23.2, R26.1, R34.1, R42.1, R43.1, R47.1, R52.1, R97.2, R100.1, TP23.1, U10.2 (3V3), Y3.4 (VDD)
+3.3VLAN: C25.1, C65.1, C66.1, C67.1, J10.01, L8.2, L9.2, Q9.3, R22.2, R29.2, R30.2, R107.1, TP16.1, U6.3 (GND)
+5V: C20.1, C21.1, C27.1, D6.1 (K), J3.01, Q1.2, R25.2, R28.2, TP21.1, U7.2 (VO)
+5VP: D6.2 (A), J2.01, Q1.1, R21.2, TP19.1
+9V: C26.1, TP22.1, U7.3 (VI)
D_Com: D15.3, R24.1, R46.1, TP13.1
ESP_EN: C32.1, D10.2 (A), D24.2, R52.2, R109.1, TP15.1, U10.3 (EN); also elsewhere on the board
GPI35: U10.7 (IO35)
GPI36/U1RXD: J8.2, R47.2, U10.4 (SENSOR_VP)
GPI39: U10.5 (SENSOR_VN)
GPIO0: D15.1, TP29.1, U6.2, U10.25 (IO0)
GPIO0/XTAL1/CLKIN: R101.1, U11.5 (XTAL1/CLKIN)
GPIO1/U0TXD: D14.1 (K), U10.35 (TXD0)
GPIO2/HS2_DATA0: D15.2, J8.4, TP28.1, U10.24 (IO2)
GPIO3/U0RXD: D13.2 (A), U10.34 (RXD0)
GPIO4/U1TXD: J8.9, U10.26 (IO4)
GPIO5/SPI_CS: J8.5, R42.2, TP30.1, U10.29 (IO5)
GPIO12/PHY_PWR: TP26.1, U10.14 (IO12)
GPIO13/I2C-SDA: J8.3, R43.2, U10.16 (IO13)
GPIO14/HS2_CLK: J8.6, U10.13 (IO14)
GPIO15/HS2_CMD: J8.7, TP27.1, U10.23 (IO15)
GPIO16/I2C-SCL: R35.1, U10.27 (IO16)
GPIO17/EMAC_CLK_OUT_180: U6.4, U10.28 (IO17)
GPIO18/MDIO(RMII): R22.1, U10.30 (IO18), U11.16 (MDIO)
GPIO19/EMAC_TXD0(RMII): U10.31 (IO19), U11.22 (TXD0)
GPIO21/EMAC_TX_EN(RMII): U10.33 (IO21), U11.21 (TXEN)
GPIO22/EMAC_TXD1(RMII): U10.36 (IO22), U11.23 (TXD1)
GPIO23/MDC(RMII): U10.37 (IO23), U11.17 (MDC)
GPIO25/EMAC_RXD0(RMII): U10.10 (IO25), U11.11 (RXD0/*MODE0)
GPIO26/EMAC_RXD1(RMII): U10.11 (IO26), U11.10 (RXD1/*MODE1)
GPIO27/EMAC_RX_CRS_DV: R29.1, U10.12 (IO27), U11.15 (COL/CRS_DV/*MODE2)
GPIO32: U10.8 (IO32)
GPIO33: R35.2, U10.9 (IO33)
LED1: U11.3 (LED1/*REGOFF); also elsewhere on the board
LED2: U11.2 (LED2/*NINTSEL); also elsewhere on the board
unnamed: C4.2, C5.2, R6.2
unnamed: C71.2, Q9.1, R97.1, R99.2, TP9.1
unnamed: D4.2 (A), R25.1
unnamed: D5.2 (A), R23.1
unnamed: D7.2 (A), R28.1
unnamed: D10.1 (K), Q4.3 (C)
unnamed: D11.2 (A), R51.1
unnamed: D13.1 (K), TP1.1, U9.30 (TXD)
unnamed: D14.2 (A), TP2.1, U9.2 (RXD)
unnamed: D24.3, R108.1
unnamed: J5.A5 (CC1), R27.1, TP3.1
unnamed: J5.B5 (CC2), R50.1, TP4.1
unnamed 47: C69.1; also elsewhere on the board
unnamed 48: R84.1; also elsewhere on the board
unnamed 49: R89.2; also elsewhere on the board
unnamed 50: J17.02, R81.1, U23.4 (I_O3); also elsewhere on the board
unnamed 51: J16.02, R33.1, U23.5 (I_O4); also elsewhere on the board
unnamed 52: J19.01, R83.1, U23.1 (I_O1); also elsewhere on the board
unnamed 53: R82.1, U11.28 (TXN), U23.3 (I_O2); also elsewhere on the board
unnamed: J8.8, R34.2
unnamed: J13.02, R104.1
unnamed: J14.02, R105.1
unnamed: J15.02, R106.1
unnamed: J18.01, J19.02
unnamed: C59.1, JP1.2 (B), R30.1, R32.2, U11.19 (NRST)
unnamed: Q4.1 (B), R41.1
unnamed: Q4.2 (E), R45.2, U9.32 (~RTS)
unnamed: Q5.1 (B), R45.1
unnamed: Q5.3 (C), R41.2, U9.31 (~DTR)
unnamed: Q5.2 (E), R46.2
unnamed: Q10.3 (D), R99.1
unnamed: R7.1, R8.2
unnamed: R24.2, R26.2, SW1.2
unnamed: C4.1, C5.1, U1.6 (COMP)
unnamed: C8.1, R7.2, U1.5 (CS)
unnamed: C7.1, U1.2 (VCC), U1.7 (DITHOFF)
unnamed: R5.2, U1.10 (RT)
unnamed: C3.1, U1.9 (SS)
unnamed: C2.1, R3.1, R4.2, U1.12 (UVLO_SYNC)
unnamed: J3.02, U4.1 (VIN), U4.3 (EN)
unnamed: J9.01, U4.5 (VOUT)
unnamed: C24.2, U9.27 (OSCI), Y1.2
unnamed: C29.2, U9.28 (OSCO), Y1.1
unnamed: J11.02, U9.15 (USBDM)
unnamed: J12.02, U9.14 (USBDP)
unnamed: J4.02, U9.1 (VCCIO), U9.19 (VCC)
unnamed: C60.1, C61.1, C62.2, TP12.1, U11.33 (EPAD)
unnamed: R31.2, U11.32 (RBIAS)
unnamed: J16.01, U11.30 (RXN)
unnamed: J17.01, U11.31 (RXP)
unnamed: J18.02, U11.29 (TXP)
unnamed: J7.01, U11.27 (VDD1A)
unnamed: J1.02, U11.1 (VDD2A)
unnamed: C63.1, C64.1, U11.6 (VDDCR)
unnamed: J10.02, U11.12 (VDDIO)
unnamed: R94.2, U12.2 (CLASS)
unnamed: R90.1, U12.3 (DET)
unnamed: R93.2, U12.1 (ILIM)
unnamed: R1.1, R2.2, TP18.1, U12.7 (UVLO)
unnamed: C72.1, R108.2, R109.2, TP25.1, U25.2 (VDD)
unnamed: R101.2, Y3.3 (OUTPUT)
OSC_DIS: Q10.1 (G), R32.1, R100.2, TP8.1, U25.1 (~RST), Y3.1 (TRI_STATE)
PHYAD0: J13.01, U11.13 (RXER/RXD4/*PHYAD0)
PHYAD1: J14.01, U11.7 (RXCLK/*PHYAD1)
PHYAD2: J15.01, U11.8 (RXD3/*PHYAD2)
RMIISEL: R107.2, TP24.1, U11.9 (RXD2/*RMIISEL)
Spare1: C1.1, C6.1, C70.1, D23.1 (A1), R1.2, R3.2, R90.2, TP11.1, U1.1 (BIAS), U12.8 (VDD); also elsewhere on the board
USB_DN: J5.A7 (DN1), J5.B7 (DN2), J11.01, TP5.1
USB_DP: J5.A6 (DP1), J5.B6 (DP2), J12.01, TP6.1
VBUS: J5.A4 (VBUS), J5.A9 (VBUS__1), J5.B4 (VBUS__2), J5.B9 (VBUS__3), Q1.3, R51.2, TP20.1
VDDA1/2: C60.2, C61.2, C62.1, C68.1, J1.01, J7.02, L8.1, R33.2, R81.2, R82.2, R83.2, R84.2, TP14.1; also elsewhere on the board

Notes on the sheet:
Ethernet
Pin
GPIO15/MTDO
Default
Debugging Log on U0TXD During Booting
Software Selectable Pins
GPIO0:
Internal Bootstrapping Resistors
General Purpose SPI
I2CEXT0_SCL_in
Rising-edge:Output
Pull-Down
3v3 LDO
JTAG
Interface
I2CEXT0_SDA_out
Pull-Up
HSPICLK_in/_out
MTDI/GPIO12:
Don't-care
VSPICLK_in/_out
Any GPIO
EMAC_COL_out
U0TXD Toggling
Falling-edge:Output
3.3V
HSPI_CS1_out
EMAC_MDI_in
HSPIQ_in/_out
VSPI_CS1_out
Rising-edge:Input
9V->5V LDO
1.8V
ESP32-WROOM
Fiducials
Download Boot
GPIO2:
EMAC
MTDO/GPIO15:
U0TXD Silent

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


Board: 4 copper layers, 101.6 x 76.2 mm, 172 parts (4 on the bottom side), 106 nets.

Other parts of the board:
J6: SI-46020-F; BEL_SI-46020-F
SW2: PTS815 SJM 250 SMTR LFS; SW4_PTS815 SJM 250 SMTR LFS_CNK

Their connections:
ESP_EN: SW2.1; also elsewhere on the board
LED1: J6.GA1; also elsewhere on the board
LED2: J6.GK2; also elsewhere on the board
unnamed 47: J6.7, J6.S1 (SHIELD), J6.S2 (SHIELD); also elsewhere on the board
unnamed 48: J6.GA2; also elsewhere on the board
unnamed 49: J6.GK1; also elsewhere on the board
unnamed 50: J6.4 (RD+); also elsewhere on the board
unnamed 51: J6.6 (RD-); also elsewhere on the board
unnamed 52: J6.1 (TD+); also elsewhere on the board
unnamed 53: J6.3 (TD-); also elsewhere on the board
Spare1: J6.10; also elsewhere on the board
VDDA1/2: J6.2 (TCT), J6.5 (RCT); also elsewhere on the board

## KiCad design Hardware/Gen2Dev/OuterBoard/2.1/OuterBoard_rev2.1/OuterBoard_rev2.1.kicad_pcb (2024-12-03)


Board: 4 copper layers, 101.6 x 76.2 mm, 224 parts (0 on the bottom side), 129 nets.

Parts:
ANT1: U.FL-R-SMT-1
C1: 6nF; C_0805_2012Metric
C2, C10, C13, C19, C20, C23, C24, C25: 10uF; C_0805_2012Metric
C3, C4, C7, C8, C11, C16, C21, C22, C26, C27: 1uF; C_0805_2012Metric
C5: 100nF; C_0603_1608Metric
C6: 10uF; CP_Radial_D5.0mm_P2.00mm
C9, C12, C34, C36, C39: 2.2uF; C_0805_2012Metric
C14, C15, C17, C32, C37, C38, C40, C42, C44: 100nF; C_0805_2012Metric
C18: 4.7uF; C_0805_2012Metric
C28, C29: 0.1uF; C_0805_2012Metric
C30, C31: 22pF; C_0402_1005Metric
C33, C35: 1.6pF; C_0402_1005Metric
C41: 10nF; C_0805_2012Metric
C43, C45: 18pF; C_0201_0603Metric
D1, D2, D3, D4, D5, D6, D8, D15: PMEG6010CEJ; D_SOD-323F
D7: B140-E3; D_SMA
D9, D10, D11, D12, D13, D14: LED; LED_0603_1608Metric
FB1: 120R-3A; C_0805_2012Metric
H1, H2, H3, H4: MountingHole; MountingHole_2.1mm
J1, J2, J3, J4, J5, J6, J9, J12, J13, J14, J15, J16, J17, J18, J19, J20, J21, J22, J23, J24, J25, J26, J27, J28, J29, J30, J31, J32, J33, J34, J35, J36, J37, J38, J39, J40, J41, J43, J45, J46, J47, J48, J49, J50, J51, J52: HMTSW-102-X-X-S-X; SAMTEC_HMTSW-102-X-X-S-X
J7, J8: 530470210; CON_530470210_MOL
J10: F32R-1A7H1-11024; AMPHENOL_F32R-1A7H1-11024
J11: 3221-10-0300-00; CONN10_3221-10-0300-00_CNC
J42: UJ31-CH-G2-SMT-TR; CUI_UJ31-CH-G2-SMT-TR
J44: 87520-0010BLF; AMPHENOL_87520-0010BLF
L1, L2: 2nH; L_0402_1005Metric
R1, R4: 2k; R_0805_2012Metric
R2, R3: 2; R_0805_2012Metric
R5, R10, R11, R12, R13, R14, R16, R17, R18, R19: 10k; R_0805_2012Metric
R6, R8: 0k; R_0805_2012Metric
R7, R9: 4.7k; R_0805_2012Metric
R15, R20, R22, R23, R24, R25: 100; R_0805_2012Metric
R26: 5.1K; R_0805_2012Metric
R27: 6.1K; R_0805_2012Metric
R31: 499; R_0805_2012Metric
SW1, SW2: PTS815 SJM 250 SMTR LFS; SW4_PTS815 SJM 250 SMTR LFS_CNK
TP1: COIL1; TestPoint_THTPad_2.0x2.0mm_Drill1.0mm
TP2: COIL2; TestPoint_THTPad_2.0x2.0mm_Drill1.0mm
TP3, TP4, TP5, TP6, TP7, TP8, TP9, TP10, TP11, TP12, TP13, TP14, TP15, TP16, TP17, TP20, TP21, TP22, TP23, TP24, TP25, TP26, TP27, TP28, TP29, TP30, TP31, TP32, TP33, TP34, TP35, TP36, TP37, TP38, TP39, TP40, TP41, TP42, TP43, TP44, TP45, TP46, TP47, TP48, TP49, TP50, TP51, TP52, TP53, TP54, TP55, TP56, TP57, TP58, TP59, TP60, TP61, TP62, TP63, TP64, TP65: TestPoint; TestPoint_Pad_D2.0mm
U1, U3: MCP73812T-420I-OT; SOT-23-5
U2: DRV8410PWPR; IC_DRV8410PWPR
U4: MIC5504-3.3YM5; SOT-23-5
U5: MIC5504-1.8YM5; SOT-23-5
U6: MCP1700x-280xxTT; SOT-23
U7: FT232RQ; QFN50P500X500X90-33N
U8: BNO055; LGA28R50P4X10_380X520X100
U9: ESP32-S3; QFN56_7X7_EXP
U11: GD25Q64CSIGR; SOP8_208MIL_GDV
XTAL1: ABS07-32.768KHZ-7-T; XTAL_ABS07-32.768KHZ-7-T_ABR
Y1: ABM8G-40.000MHZ-18-D2Y-T; CRYSTAL_ABM8G_ABR

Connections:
+1V8: C24.1, C26.1, J10.10, J22.02, R23.2, TP48.1
+2V8: C9.1, C27.1, D7.2 (A), FB1.1, J10.11, R6.2, TP42.1, TP49.1, TP63.1
+3.3V: C13.1, C16.1, C17.1, C18.1, C23.1, C28.1, C32.1, C34.1, C36.1, C37.1, C39.1, C40.1, C41.1, C42.1, J11.5, J20.02, J33.02, J35.01, J38.01, L2.1, R8.2, R10.1, R11.1, R12.1, R13.1, R14.1, R15.2, R19.1, R22.2, TP12.1, TP38.1, U8.4 (NBOOT_LOAD_PIN), U9.20 (VDD3P3_RTC), U9.46 (VDD3P3_CPU)
+5V: J36.01, J42.A4 (VBUS), J42.A9 (VBUS__1), J42.B4 (VBUS__2), J42.B9 (VBUS__3), J44.1 (VCC), J45.01, R20.2, R25.2
+BATT: C4.1, C5.1, C6.1, C8.1, D5.2 (A), J12.01, J13.01, J23.02, TP3.1, U1.3 (V_{BAT}), U3.3 (V_{BAT})
BNO_INT: J25.01, U8.14 (INT)
BNO_SCL: J26.01, R11.2, U8.19 (COM1)
BNO_SDA: J27.01, R12.2, U8.20 (COM0)
CAM_RESET: C15.1, J10.6, R10.2, TP44.1
CHIP_EN: J11.6, SW1.1, TP20.1, U9.4 (CHIP_PU)
D0/A0: J31.01, U9.6 (GPIO1)
D1/A1: J30.01, U9.7 (GPIO2)
D2/A2: J29.01, U9.8 (GPIO3)
D3/A3: J28.01, U9.9 (GPIO4)
DRV_FAULT: J16.01, R19.2, TP11.1, U2.8 (~FAULT)
DRV_SLEEP: J24.01, U2.1 (~SLEEP)
GND: ANT1.GND1, ANT1.GND2, C1.2, C2.2, C3.2, C4.2, C5.2, C6.2, C7.2, C8.2, C9.2, C10.2, C11.2, C12.2, C13.2, C14.2, C15.2, C16.2, C17.2, C18.2, C19.2, C20.2, C21.2, C22.2, C23.2, C24.2, C25.2, C26.2, C27.2, C28.2, C29.2, C30.2, C31.2, C32.2, C33.2, C34.2, C35.2, C36.2, C37.2, C38.2, C39.2, C40.2, C41.2, C42.2, C43.2, C44.2, C45.2, D10.1 (K), D11.1 (K), D12.1 (K), D13.1 (K), D14.1 (K), J4.01, J7.2, J8.2, J10.2, J10.15, J10.23, J11.3, J11.4, J39.01, J40.01, J41.01, J42.A1 (GND), J42.A12 (GND__1), J42.B1 (GND__2), J42.B12 (GND__3), J42.SH1 (SHIELD), J42.SH2 (SHIELD__1), J42.SH3 (SHIELD__2), J42.SH4 (SHIELD__3), J44.4 (GND), J44.SH1 (SHIELD), J44.SH2 (SHIELD__1), R1.2, R2.2, R3.2, R4.2, R5.2, R16.2, R17.2, R18.2, R26.2, R27.2, SW1.4, SW2.4, TP37.1, TP39.1, TP53.1, TP61.1, U1.2 (V_{SS}), U2.13 (GND), U2.17 (EXP), U3.2 (V_{SS}), U4.2 (GND), U5.2 (GND), U6.1 (GND), U7.4 (GND), U7.17 (GND), U7.20 (GND), U7.24 (AGND), U8.2 (GND), U8.18 (COM2), U8.25 (GNDIO), U9.57 (GND), U11.4 (VSS), Y1.2 (GND), Y1.4 (GND)
GPIO0: SW2.1, U9.5 (GPIO0)
GPIO33: J27.02, U9.38 (GPIO33)
GPIO34: J26.02, U9.39 (GPIO34)
GPIO35: J25.02, U9.40 (GPIO35)
GPIO36: J24.02, U9.41 (GPIO36)
GPIO37: J16.02, U9.42 (GPIO37)
IO10/XMCLK: J10.13, TP51.1, U9.15 (GPIO10)
IO11/DVP_Y8: J10.14, TP52.1, U9.16 (GPIO11)
IO12/DVP_Y7: J10.16, TP54.1, U9.17 (GPIO12)
IO13/DVP_PCLK: J10.17, TP55.1, U9.18 (GPIO13)
IO14/DVP_Y6: J10.18, TP56.1, U9.19 (GPIO14)
IO15/DVP_Y2: J10.19, TP57.1, U9.21 (XTAL_32K_P)
IO16/DVP_Y5: J10.20, TP58.1, U9.22 (XTAL_32K_N)
IO17/DVP_Y3: J10.21, TP59.1, U9.23 (GPIO17)
IO18/DVP_Y4: J10.22, TP60.1, U9.24 (GPIO18)
IO21/USER_LED: D9.1 (K), TP27.1, U9.27 (GPIO21)
IO38/DVP_VSYNC: J10.7, TP45.1, U9.43 (GPIO38)
IO47/DVP_HREF: J10.9, TP47.1, U9.37 (SPICLK_P)
IO48/DVP_Y9: J10.12, TP50.1, U9.36 (SPICLK_N)
MOTOR1_AIN1: J28.02, U2.16 (AIN1)
MOTOR1_AIN2: J29.02, U2.15 (AIN2)
MOTOR2_BIN1: J30.02, U2.9 (BIN1)
MOTOR2_BIN2: J31.02, U2.10 (BIN2)
MTCK/IO39/CAM_SCL: J10.5, J11.7, R9.2, TP21.1, TP43.1, U9.44 (MTCK)
MTDI/IO41/PDM_DATA: J11.9, TP23.1, U9.47 (MTDI)
MTDO/IO40/CAM_SDA: J10.3, J11.8, R7.2, TP22.1, TP40.1, U9.45 (MTDO)
MTMS/IO42/PDM_CLK: J11.10, TP24.1, U9.48 (MTMS)
unnamed: ANT1.SIG, C33.1, L1.2
unnamed: C25.1, J21.02, R24.2
unnamed: C38.1, J32.01, L2.2
unnamed: D1.2 (A), D2.2 (A), J4.02
unnamed: D1.1 (K), D3.2 (A), J1.02
unnamed: D2.1 (K), D4.2 (A), J2.01
unnamed: D3.1 (K), D4.1 (K), J3.01
unnamed: C12.1, C14.1, D7.1 (K), J10.24, TP62.1
unnamed: D8.2 (A), J36.02
unnamed: D8.1 (K), J37.01
unnamed: D9.2 (A), R15.1
unnamed: D10.2 (A), R22.1
unnamed: D11.2 (A), R23.1
unnamed: D12.2 (A), R24.1
unnamed: D13.2 (A), R25.1
unnamed: D14.2 (A), R20.1
unnamed: D15.2 (A), J45.02
unnamed: D15.1 (K), J46.01
unnamed: FB1.2, J10.4, TP41.1
unnamed: J1.01, TP1.1
unnamed: J2.02, TP2.1
unnamed: J10.8, R5.1, TP46.1
unnamed: J7.1, J12.02
unnamed: J8.1, J13.02
unnamed: J32.02, U9.2 (VDD3P3), U9.3 (VDD3P3)
unnamed: J33.01, U9.55 (VDDA), U9.56 (VDDA)
unnamed: J42.A5 (CC1), R26.1, TP64.1
unnamed: J42.B5 (CC2), R27.1, TP65.1
unnamed: J42.A6 (DP1), J42.A7 (DN1), J49.01, TP25.1
unnamed: J42.B6 (DP2), J42.B7 (DN2), J50.02, TP26.1
unnamed: J44.3 (D+), J48.02
unnamed: J44.2 (D-), J47.01
unnamed: R6.1, R7.1, R8.1, R9.1
unnamed: R13.2, SW1.2
unnamed: R14.2, SW2.2
unnamed: R1.1, TP7.1, U1.5 (PROG)
unnamed: J14.02, U1.4 (V_{DD})
unnamed: R3.1, TP9.1, U2.3 (AISEN)
unnamed: J6.01, U2.2 (AOUT1)
unnamed: J6.02, U2.4 (AOUT2)
unnamed: R2.1, TP8.1, U2.6 (BISEN)
unnamed: J5.01, U2.7 (BOUT1)
unnamed: J5.02, U2.5 (BOUT2)
unnamed: J23.01, U2.12 (VM)
unnamed: R4.1, TP10.1, U3.5 (PROG)
unnamed: J15.02, U3.4 (V_{DD})
unnamed: J17.02, U4.1 (VIN), U4.3 (EN)
unnamed: J20.01, U4.5 (VOUT)
unnamed: J18.02, U5.1 (VIN), U5.3 (EN)
unnamed: J22.01, U5.5 (VOUT)
unnamed: J19.02, U6.3 (VI)
unnamed: J21.01, U6.2 (VO)
unnamed: J52.02, U7.2 (RXD)
unnamed: J51.01, U7.30 (TXD)
unnamed: J43.01, U7.15 (USBDM)
unnamed: J9.02, U7.14 (USBDP)
unnamed: J35.02, U7.1 (VCCIO), U7.19 (VCC)
unnamed: C29.1, TP36.1, U8.9 (CAP)
unnamed: R18.1, TP35.1, U8.17 (COM3)
unnamed: J39.02, U8.10 (PIN10)
unnamed: J40.02, U8.15 (PIN15)
unnamed: J41.02, U8.16 (PIN16)
unnamed: R17.1, TP33.1, U8.6 (PS0)
unnamed: R16.1, TP34.1, U8.5 (PS1)
unnamed: J38.02, U8.3 (VDD), U8.28 (VDDIO)
unnamed: C30.1, TP31.1, U8.27 (XIN32), XTAL1.2
unnamed: C31.1, TP32.1, U8.26 (XOUT32), XTAL1.1
unnamed: C35.1, L1.1, U9.1 (LNA_IN)
unnamed: R31.1, U9.49 (U0TXD)
unnamed: C45.1, TP14.1, U9.53 (XTAL_N), Y1.1
unnamed: C43.1, TP13.1, U9.54 (XTAL_P), Y1.3
unnamed: J34.01, U11.8 (VCC)
RX_D7: J51.02, U9.50 (U0RXD)
SPICLK: TP16.1, U9.33 (SPICLK), U11.6 (SCLK)
SPICS0: TP17.1, U9.32 (SPICS0), U11.1 (CS#)
SPID: TP30.1, U9.35 (SPID), U11.5 (SI(IO0))
SPIHD: TP15.1, U9.30 (SPIHD), U11.7 (HOLD#(IO3))
SPIQ: TP28.1, U9.34 (SPIQ), U11.2 (SO(IO1))
SPIWP: TP29.1, U9.31 (SPIWP), U11.3 (WP#(IO2))
TX_D6: J52.01, R31.2
USB_DN: J43.02, J47.02, J49.02, U9.25 (GPIO19)
USB_DP: J9.01, J48.01, J50.01, U9.26 (GPIO20)
VCC: C1.1, C2.1, C3.1, C7.1, D6.2 (A), J3.02, J14.01, J15.01, TP5.1, U1.1 (CE), U3.1 (CE)
VDC: C10.1, C11.1, C19.1, C20.1, C21.1, C22.1, D5.1 (K), D6.1 (K), J17.01, J18.01, J19.01, J37.02, J46.02, TP4.1, TP6.1
VDD_SPI: C44.1, J34.02, U9.29 (VDD_SPI)

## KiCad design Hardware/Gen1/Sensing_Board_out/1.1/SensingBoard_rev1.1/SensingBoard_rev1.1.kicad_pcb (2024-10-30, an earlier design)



Board: 6 copper layers, 40.0 x 40.0 mm, 89 parts (15 on the bottom side), 74 nets.

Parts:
ANT1: U.FL-R-SMT-1
C1, C2, C4, C18, C29, C30, C34, C36, C37: 100nF; C_0402_1005Metric
C3: 4.7uF; C_0402_1005Metric
C5, C7, C13, C19, C21, C23, C25: 10uF; C_0603_1608Metric
C6, C8, C20, C22, C24, C26: 1uF; C_0201_0603Metric
C9, C10: 0.1uF; C_0603_1608Metric
C11, C12: 22pF; C_0201_0603Metric
C14, C15: 1.6pF; C_0402_1005Metric
C16, C17: 18pF; C_0201_0603Metric
C27, C28, C31, C32, C33: 2.2uF; C_0402_1005Metric
C35: 10nF; C_0402_1005Metric
D2: LED; LED_0603_1608Metric
D3: PMEG6010CEJ; D_SOD-323F
D4: B140-E3; D_SMA
FB1: 120R-3A; C_0805_2012Metric
J1: USB_C_Receptacle; USB_C_Receptacle_Molex_105450-0101-L
J2: 3221-10-0300-00; CONN10_3221-10-0300-00_CNC
J3: F32R-1A7H1-11024; AMPHENOL_F32R-1A7H1-11024
J5, J6, J7, J9: RS1-02-G; CONN_RS1-02-G_ADM
L1, L2: 2nH; L_0201_0603Metric
R1: 100; R_0201_0603Metric
R3: 6.1K; R_0201_0603Metric
R4: 5.1K; R_0201_0603Metric
R5, R6, R7, R8, R11, R12, R13, R21, R24, R25: 10k; R_0201_0603Metric
R9, R10, R14, R15, R16, R17, R18, R19, R20, R22, R27: 0k; R_0201_0603Metric
R23, R28: 4.7k; R_0201_0603Metric
R26: 499; R_0201_0603Metric
SW1, SW2: PTS815 SJM 250 SMTR LFS; SW4_PTS815 SJM 250 SMTR LFS_CNK
U2: BNO055; LGA28R50P4X10_380X520X100
U3: MIC5504-3.3YM5; SOT-23-5
U4: FT232RQ; QFN50P500X500X90-33N
U5: MIC5504-1.8YM5; SOT-23-5
U6: MCP1700x-280xxTT; SOT-23
U7: ESP32-S3; QFN56_7X7_EXP
U8: GD25D05CT; SOP-8_3.9x4.9mm_P1.27mm
XTAL2: ABS07-32.768KHZ-7-T; XTAL_ABS07-32.768KHZ-7-T_ABR
Y1: ABM8G-40.000MHZ-18-D2Y-T; CRYSTAL_ABM8G_ABR

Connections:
+1V8: C21.1, C22.1, J3.10, U5.5 (VOUT)
+2V8: C25.1, C26.1, C27.1, D4.2 (A), FB1.1, J3.11, R22.2, U6.2 (VO)
+3.3V: C2.1, C3.1, C4.1, C7.1, C8.1, C9.1, C13.1, C30.1, C31.1, C32.1, C33.1, C34.1, C35.1, C36.1, C37.1, J2.5, L2.1, R1.2, R5.1, R11.1, R12.1, R13.1, R21.1, R24.1, R27.2, U2.3 (VDD), U2.4 (NBOOT_LOAD_PIN), U2.28 (VDDIO), U3.5 (VOUT), U4.1 (VCCIO), U4.19 (VCC), U7.20 (VDD3P3_RTC), U7.46 (VDD3P3_CPU), U7.55 (VDDA), U7.56 (VDDA), U8.8 (VCC)
+5V: D3.2 (A), J1.A4 (VBUS), J1.A9 (VBUS), J1.B4 (VBUS), J1.B9 (VBUS)
BNO_INT: R14.1, U2.14 (INT)
BNO_SCL: R12.2, R19.1, U2.19 (COM1)
BNO_SDA: R13.2, R20.1, U2.20 (COM0)
CAM_RESET: C1.1, J3.6, R24.2
CHIP_EN: J2.6, SW1.1, U7.4 (CHIP_PU)
D0/A0: R17.2, U7.6 (GPIO1)
D1/A1: R16.2, U7.7 (GPIO2)
D2/A2: R15.2, U7.8 (GPIO3)
D3/A3: R10.2, U7.9 (GPIO4)
DRV_FAULT: J7.1, R11.2, R18.1
DRV_SLEEP: J7.2, R9.1
GND: ANT1.GND1, ANT1.GND2, C1.2, C2.2, C3.2, C4.2, C5.2, C6.2, C7.2, C8.2, C9.2, C10.2, C11.2, C12.2, C13.2, C14.2, C15.2, C16.2, C17.2, C18.2, C19.2, C20.2, C21.2, C22.2, C23.2, C24.2, C25.2, C26.2, C27.2, C28.2, C29.2, C30.2, C31.2, C32.2, C33.2, C34.2, C35.2, C36.2, C37.2, J1.A1 (GND), J1.A12 (GND), J1.B1 (GND), J1.B12 (GND), J1.S1 (SHIELD), J2.3, J2.4, J3.2, J3.15, J3.23, J9.1, R3.2, R4.2, R6.2, R7.2, R8.2, R25.2, SW1.4, SW2.4, U2.2 (GND), U2.10 (PIN10), U2.15 (PIN15), U2.16 (PIN16), U2.18 (COM2), U2.25 (GNDIO), U3.2 (GND), U4.4 (GND), U4.17 (GND), U4.20 (GND), U4.24 (AGND), U5.2 (GND), U6.1 (GND), U7.57 (GND), U8.4 (VSS), Y1.2 (GND), Y1.4 (GND)
GPIO0: SW2.1, U7.5 (GPIO0)
GPIO33: R20.2, U7.38 (GPIO33)
GPIO34: R19.2, U7.39 (GPIO34)
GPIO35: R14.2, U7.40 (GPIO35)
GPIO36: R9.2, U7.41 (GPIO36)
GPIO37: R18.2, U7.42 (GPIO37)
IO10/XMCLK: J3.13, U7.15 (GPIO10)
IO11/DVP_Y8: J3.14, U7.16 (GPIO11)
IO12/DVP_Y7: J3.16, U7.17 (GPIO12)
IO13/DVP_PCLK: J3.17, U7.18 (GPIO13)
IO14/DVP_Y6: J3.18, U7.19 (GPIO14)
IO15/DVP_Y2: J3.19, U7.21 (XTAL_32K_P)
IO16/DVP_Y5: J3.20, U7.22 (XTAL_32K_N)
IO17/DVP_Y3: J3.21, U7.23 (GPIO17)
IO18/DVP_Y4: J3.22, U7.24 (GPIO18)
IO21/USER_LED: D2.1 (K), U7.27 (GPIO21)
IO38/DVP_VSYNC: J3.7, U7.43 (GPIO38)
IO47/DVP_HREF: J3.9, U7.37 (SPICLK_P)
IO48/DVP_Y9: J3.12, U7.36 (SPICLK_N)
MOTOR1_AIN1: J5.2, R10.1
MOTOR1_AIN2: J5.1, R15.1
MOTOR2_BIN1: J6.2, R16.1
MOTOR2_BIN2: J6.1, R17.1
MTCK/IO39/CAM_SCL: J2.7, J3.5, R28.2, U7.44 (MTCK)
MTDI/IO41/PDM_DATA: J2.9, U7.47 (MTDI)
MTDO/IO40/CAM_SDA: J2.8, J3.3, R23.2, U7.45 (MTDO)
MTMS/IO42/PDM_CLK: J2.10, U7.48 (MTMS)
unnamed: ANT1.SIG, C15.1, L1.2
unnamed: C18.1, L2.2, U7.2 (VDD3P3), U7.3 (VDD3P3)
unnamed: D2.2 (A), R1.1
unnamed: C28.1, C29.1, D4.1 (K), J3.24
unnamed: FB1.2, J3.4
unnamed: J1.A5 (CC1), R4.1
unnamed: J1.B5 (CC2), R3.1
unnamed: J3.8, R25.1
unnamed: R5.2, SW1.2
unnamed: R21.2, SW2.2
unnamed: R22.1, R23.1, R27.1, R28.1
unnamed: C10.1, U2.9 (CAP)
unnamed: R6.1, U2.17 (COM3)
unnamed: R8.1, U2.6 (PS0)
unnamed: R7.1, U2.5 (PS1)
unnamed: C12.1, U2.27 (XIN32), XTAL2.2
unnamed: C11.1, U2.26 (XOUT32), XTAL2.1
unnamed: C14.1, L1.1, U7.1 (LNA_IN)
unnamed: R26.1, U7.49 (U0TXD)
unnamed: C17.1, U7.53 (XTAL_N), Y1.1
unnamed: C16.1, U7.54 (XTAL_P), Y1.3
RX_D7: U4.30 (TXD), U7.50 (U0RXD)
SPICLK: U7.33 (SPICLK), U8.6 (SCLK)
SPICS0: U7.32 (SPICS0), U8.1 (~CS)
SPID: U7.35 (SPID), U8.5 (SI/IO0)
SPIQ: U7.34 (SPIQ), U8.2 (O1/SO)
SPIWP: U7.31 (SPIWP), U8.3 (~WP)
TX_D6: R26.2, U4.2 (RXD)
USB_DN: J1.A7 (D-), J1.B7 (D-), U4.15 (USBDM), U7.25 (GPIO19)
USB_DP: J1.A6 (D+), J1.B6 (D+), U4.14 (USBDP), U7.26 (GPIO20)
VDC: C5.1, C6.1, C19.1, C20.1, C23.1, C24.1, D3.1 (K), J9.2, U3.1 (VIN), U3.3 (EN), U5.1 (VIN), U5.3 (EN), U6.3 (VI)

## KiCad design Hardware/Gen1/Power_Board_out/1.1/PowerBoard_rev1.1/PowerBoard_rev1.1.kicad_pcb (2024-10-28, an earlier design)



Board: 4 copper layers, 40.0 x 40.0 mm, 31 parts (4 on the bottom side), 20 nets.

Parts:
C1: 100nF; C_0603_1608Metric
C2: 10uF; CP_Radial_D5.0mm_P2.00mm
C5, C6, C7, C8: 1uF; C_0603_1608Metric
C11: 6nF; C_0805_2012Metric
C12: 10uF; C_0805_2012Metric
D5, D6, D11, D12, D13, D14: PMEG6010CEJ; D_SOD-323F
J1, J2, J3, J4, J5, J6: HMTSW-102-X-X-S-X; SAMTEC_HMTSW-102-X-X-S-X
J7, J8: 530470210; CON_530470210_MOL
R1, R2: 2k; R_0805_2012Metric
R3, R4: 2; R_0805_2012Metric
TP5: COIL1; TestPoint_THTPad_2.0x2.0mm_Drill1.0mm
TP6: COIL2; TestPoint_THTPad_2.0x2.0mm_Drill1.0mm
U1: DRV8410PWPR; IC_DRV8410PWPR
U2, U3: MCP73812T-420I-OT; SOT-23-5

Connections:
+BATT: C1.1, C2.1, C6.1, C8.1, D5.2 (A), J7.1, J8.1, U1.12 (VM), U2.3 (V_{BAT}), U3.3 (V_{BAT})
DRV_FAULT: J6.01, U1.8 (~FAULT)
DRV_SLEEP: J6.02, U1.1 (~SLEEP)
GND: C1.2, C2.2, C5.2, C6.2, C7.2, C8.2, C11.2, C12.2, D11.2 (A), D12.2 (A), J3.01, J7.2, J8.2, R1.2, R2.2, R3.2, R4.2, U1.13 (GND), U1.17 (EXP), U2.2 (V_{SS}), U3.2 (V_{SS})
MOTOR1_AIN1: J4.02, U1.16 (AIN1)
MOTOR1_AIN2: J4.01, U1.15 (AIN2)
MOTOR2_BIN1: J5.02, U1.9 (BIN1)
MOTOR2_BIN2: J5.01, U1.10 (BIN2)
unnamed: D11.1 (K), D13.2 (A), TP5.1
unnamed: D12.1 (K), D14.2 (A), TP6.1
unnamed: R3.1, U1.3 (AISEN)
unnamed: J2.01, U1.2 (AOUT1)
unnamed: J2.02, U1.4 (AOUT2)
unnamed: R4.1, U1.6 (BISEN)
unnamed: J1.01, U1.7 (BOUT1)
unnamed: J1.02, U1.5 (BOUT2)
unnamed: R1.1, U2.5 (PROG)
unnamed: R2.1, U3.5 (PROG)
VCC: C5.1, C7.1, C11.1, C12.1, D6.2 (A), D13.1 (K), D14.1 (K), U2.1 (CE), U2.4 (V_{DD}), U3.1 (CE), U3.4 (V_{DD})
VDC: D5.1 (K), D6.1 (K), J3.02

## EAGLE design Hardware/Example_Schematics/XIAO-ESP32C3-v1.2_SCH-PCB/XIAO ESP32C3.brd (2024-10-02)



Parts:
ANT: U.FL-R-SMT-1; U-FL3P-SMD-2.6X2.6X1.0MM
BAT: DNP; TP-80X40MIL
BOOT: TD-1183SN-A3N-D1R; BUTTON_TD1183SA
C1, C4, C23, C39, C40, C43, C54: 2.2uF; C0201
C2, C44: 1uF; C0201
C3, C5, C7, C10, C45, C50, C53: 100nF; C0201
C6: 10pF; C0201
C8, C9, C41, C42: 18pF; C0201
C11, C12, C13: DNP; C0201
C14, C48: 1.6pF; C0201
C15, C49: 0R; C0201
CHG: RED; LED-0402
D1: MSK4005; SOD-523
F1: 6V_500mA_Fuse; F0603
GND: DNP; TP-80X40MIL
J1, J2: DNP; H7-HALF-HOLE-2.54
L1, L3: 2nH; L0201
Q1: LP0404N3T5G; PMOS_1.0*0.6*0.35MM
R1, R2: 5.1k; R0201
R3, R21: DNP; R0201
R4, R6: 10k; R0201
R5: 1R; R0201
R7, R32: 0R; R0201
R8, R10: 22R; R0201
R9: 100k; R0201
R22: 2.7k; R0201
R31: 2.2k; R0201
RST: TD-1183SN-A3N-D1R; BUTTON_TD1183SA
TP1, TP2, TP3, TP4, TP5, TP6: DNP; TP-D45MIL
U1: PMIC-XC6802MR; SOT-25
U2: XC6210B332MR; SOT-25
U4: ESP32-C3FN4; QFN32G-0.5-5X5MM
USB: UBF31-0171; USB2.0-TYPE-C
X2: 32.768k/9KAA32768122TF90QT; X2-SMD-1.6X1.0X0.5MM
X4: 40MHz/306011037; X4-SMD-2.0X1.6X0.5MM

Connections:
32K_N: C9.1, U4.5 (XTAL_32K_N), X2.1
32K_P: R7.1, U4.4 (XTAL_32K_P)
!CHG: CHG.-, R21.1, U1.1 (/CHG)
D0: J2.1, J2.13 (1), U4.6 (GPIO2)
D1: J2.2, J2.14 (2), U4.8 (GPIO3)
D2: J2.3, J2.15 (3), TP2.T, U4.9 (MTMS)
D3: J2.4, J2.16 (4), TP3.T, U4.10 (MTDI)
D4: J2.5, J2.17 (5), TP4.T, U4.12 (MTCK)
D5: J2.6, J2.18 (6), TP5.T, U4.13 (MTDO)
D8: J1.2, J1.14 (2), U4.14 (GPIO8)
D9: BOOT.2, C6.2, J1.3, J1.15 (3), R6.1, U4.15 (GPIO9)
D10: J1.4, J1.16 (4), U4.16 (GPIO10)
DM: R10.1, USB.A7 (A7/DN1), USB.B7 (B7/DN2)
DP: R8.1, USB.A6 (A6/DP1), USB.B6 (B6/DP2)
EN: C5.2, R4.1, RST.2, TP6.T, U4.7 (CHIP_EN)
ESP_USB_DM: C11.2, R10.2, U4.25 (GPIO18)
ESP_USB_DP: C12.2, R8.2, U4.26 (GPIO19)
GND: ANT.GND1, ANT.GND2, BOOT.1, C1.2, C2.1, C3.1, C4.2, C5.1, C6.1, C7.1, C8.2, C9.2, C10.1, C11.1, C12.1, C13.1, C14.1, C23.1, C39.1, C40.2, C41.2, C42.2, C43.1, C44.1, C45.1, C48.1, C50.1, C53.1, C54.1, GND.1, J1.6, J1.18 (6), R1.1, R2.2, R9.1, R21.2, R22.2, RST.1, TP1.T, U1.2 (VSS), U2.2 (VSS), U4.33 (PAD), USB.A1_B12 (A1/B12/GND), USB.B1_A12 (B1/A12/GND), USB.S1, USB.S2, USB.S3, USB.S4, USB.S5 (S1), USB.S6 (S2), X4.2 (GND), X4.4 (GND)
unnamed: R2.1, USB.A5 (A5/CC1)
unnamed: R1.2, USB.B5 (B5/CC2)
unnamed: R3.1, U4.21 (SPICS0)
unnamed: C8.1, R7.2, X2.2
unnamed: C13.2, U2.4 (NC)
unnamed: C15.2, C49.1
unnamed: R22.1, U1.5 (ISEN)
unnamed: CHG.+, R31.2
unnamed: C14.2, C15.1, L1.2, U4.1 (LNA_IN)
unnamed: C41.1, R32.2, X4.3 (X2)
unnamed: C42.1, U4.29 (XTAL_N), X4.1 (X1)
unnamed: ANT.D, C48.2, C49.2, L1.1
unnamed: R5.2, U4.28 (U0TXD)
unnamed: C50.2, L3.2, U4.2 (VDD3P3), U4.3 (VDD3P3)
unnamed: R32.1, U4.30 (XTAL_P)
RX_D7: J1.1, J1.13 (1), U4.27 (U0RXD)
TX_D6: J2.7, J2.19 (7), R5.1
USB_FUSED_5V: C10.2, C39.2, D1.+, F1.2, Q1.2 (G), R9.2, U1.4 (VIN)
VBAT: BAT.1, C40.1, Q1.1 (D), U1.3 (BAT)
VCC_3V3: C2.2, C3.2, C7.2, C23.2, C43.2, C44.2, C45.2, C53.2, C54.2, J1.5, J1.17 (5), L3.1, R4.2, R6.2, R31.1, U2.5 (VOUT), U4.11 (VDD3P3_RTC), U4.17 (VDD3P3_CPU), U4.31 (VDDA), U4.32 (VDDA)
VDD_SPI: R3.2, U4.18 (VDD_SPI)
VIN: C1.1, C4.1, D1.-, Q1.3 (S), U2.1 (VIN), U2.3 (CE)
VUSB: F1.1, J1.7, J1.19 (7), USB.A4_B9 (A4/B9/VBUS), USB.B4_A9 (B4/A9/VBUS)

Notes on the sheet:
1.0
First release
2021.01.11
Bruce
700mA



Board: 4 copper layers, 21.0 x 17.8 mm, 68 parts (9 on the bottom side), 41 nets.

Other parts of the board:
U$2: LOGO-SEEED-NEW-1X9.6MM

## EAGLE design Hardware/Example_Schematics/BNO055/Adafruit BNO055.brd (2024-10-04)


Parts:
C1, C2: 22pF; 0805-NO
C3: 0.1uF; 0805-NO
C4: 0.1uF; 0805_10MGAP
C5: 10uF; 0805-NO
C6: 10uF; 0805_10MGAP
D1: 1n4148; SOD-323
FID1, FID2: FIDUCIAL""; FIDUCIAL_1MM
JP1: HEADER-1X676MIL; 1X06_ROUND_76
JP2: HEADER-1X476MIL; 1X04_ROUND_76
Q1, Q2: BSS138; SOT23-WIDE
R3, R4, R5, R6, R7, R10: 10K; 0805-NO
R8, R9: 10K; _0805MP
U1: MIC5225-3.3; SOT23-5
U$2: BNO055
U$29, U$30, U$31, U$32: MOUNTINGHOLE2.5_THICK; MOUNTINGHOLE_2.5_PLATED_THICK
Y1: 32.768kHz; CRYSTAL_8X3.8

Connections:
3.3V: C4.2, C6.1, JP1.2, Q1.1 (G), Q2.1 (G), R6.2, R7.2, R10.2, U1.5 (OUT), U$2.3 (VDD), U$2.4 (NBOOT_LOAD_PIN), U$2.28 (VDDIO)
5.0V: C5.1, JP1.1, R8.2, R9.2, U1.1 (IN), U1.3 (EN)
GND: C1.1, C2.1, C3.1, C4.1, C5.2, C6.2, JP1.3, R3.2, R4.2, R5.2, U1.2 (GND), U$2.2 (GND), U$2.10 (PIN10(GND)), U$2.15 (PIN15(GND)), U$2.16 (PIN16(GND)), U$2.18 (COM2(GND)), U$2.25 (GND)
I2CADDR_3V: JP2.4, R5.1, U$2.17 (COM3/I2C_ADDR)
INT_3V: JP2.3, U$2.14 (INT)
unnamed: C1.2, U$2.27 (XIN32), Y1.P$4 (2)
unnamed: C2.2, U$2.26 (XOUT32), Y1.P$1 (1)
unnamed: C3.2, U$2.9 (CAP)
NRESET_3V: D1.A, R10.1, U$2.11 (NRESET)
PS0_3V: JP2.1, R3.1, U$2.6 (PS0)
PS1_3V: JP2.2, R4.1, U$2.5 (PS1)
RST_5V: D1.C, JP1.6
SCL_3V: Q2.2 (S), R7.1, U$2.19 (COM1/SCL/RX)
SCL_5V: JP1.5, Q2.3 (D), R9.1
SDA_3V: Q1.2 (S), R6.1, U$2.20 (COM0/SDA/TX)
SDA_5V: JP1.4, Q1.3 (D), R8.1



Board: 2 copper layers, 26.7 x 20.3 mm, 31 parts (2 on the bottom side), 16 nets.

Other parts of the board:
U$3: PCBFEAT-REV-040
U$28: ADAFRUIT_TEXT_20MM
U$33: ADAFRUIT_2.5MM

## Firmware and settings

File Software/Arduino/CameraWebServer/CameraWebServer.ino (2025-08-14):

#include <Wire.h>
#include "esp_camera.h"
#include <WiFi.h>
#include "imu_function.h"
#include <ESP32Servo.h>

//
// WARNING!!! PSRAM IC required for UXGA resolution and high JPEG quality
//            Ensure ESP32 Wrover Module or other board with PSRAM is selected
//            Partial images will be transmitted if image exceeds buffer size
//
//            You must select partition scheme from the board menu that has at least 3MB APP space.
//            Face Recognition is DISABLED for ESP32 and ESP32-S2, because it takes up from 15
//            seconds to process single frame. Face Detection is ENABLED if PSRAM is enabled as well

// ===================
// Select camera model
// ===================
//#define CAMERA_MODEL_WROVER_KIT // Has PSRAM
// #define CAMERA_MODEL_ESP_EYE  // Has PSRAM
//#define CAMERA_MODEL_ESP32S3_EYE // Has PSRAM
//#define CAMERA_MODEL_M5STACK_PSRAM // Has PSRAM
//#define CAMERA_MODEL_M5STACK_V2_PSRAM // M5Camera version B Has PSRAM
//#define CAMERA_MODEL_M5STACK_WIDE // Has PSRAM
//#define CAMERA_MODEL_M5STACK_ESP32CAM // No PSRAM
//#define CAMERA_MODEL_M5STACK_UNITCAM // No PSRAM
//#define CAMERA_MODEL_M5STACK_CAMS3_UNIT  // Has PSRAM
// #define CAMERA_MODEL_AI_THINKER // Has PSRAM
//#define CAMERA_MODEL_TTGO_T_JOURNAL // No PSRAM
#define CAMERA_MODEL_XIAO_ESP32S3 // Has PSRAM
// ** Espressif Internal Boards **
//#define CAMERA_MODEL_ESP32_CAM_BOARD
//#define CAMERA_MODEL_ESP32S2_CAM_BOARD
//#define CAMERA_MODEL_ESP32S3_CAM_LCD
//#define CAMERA_MODEL_DFRobot_FireBeetle2_ESP32S3 // Has PSRAM
//#define CAMERA_MODEL_DFRobot_Romeo_ESP32S3 // Has PSRAM
#include "camera_pins.h"

// ===========================
// Enter your WiFi credentials
// ===========================
// const char *ssid = "Vcc-AP";
// const char *password = "12345678";

const char *ssid = "NETGEAR42";
const char *password = "cleverroad877";

extern int led_pin_state;
const int led_pin1 = 5;
const int led_pin2 = 6;
const int ledPin = 21; // On-board LED on GPIO21
int ledState = 0;

imu_function imu_func;

extern Servo myServo1;  // Create servo object
extern Servo myServo2;  // Create servo object
const int servoPin1 = 2;  // GPIO pin for the servo signal (adjust as needed)
const int servoPin2 = 45;  // GPIO pin for the servo signal (adjust as needed)

int servoAngle1 = 0; // 0 for right, 1 for left
int servoCounter1 = 0;
int servoAngle2 = 0; // 0 for right, 1 for left
int servoCounter2 = 0;

void startCameraServer();
void setupLedFlash(int pin);


// Function to handle WiFi events
void WiFiEvent(WiFiEvent_t event) {
  switch (event) {
    case ARDUINO_EVENT_WIFI_STA_DISCONNECTED:
      Serial.println("WiFi disconnected! Attempting reconnection...");
      WiFi.begin(ssid, password);
      break;

    case ARDUINO_EVENT_WIFI_STA_CONNECTED:
      Serial.println("WiFi connected!");
      break;

    case ARDUINO_EVENT_WIFI_STA_GOT_IP:
      Serial.print("WiFi reconnected! New IP address: ");
      Serial.println(WiFi.localIP());
      break;

    default:
      break;
  }
}

void setup() {
  Wire.begin(3, 4); //Comment out if using XIAO sense, diff SDA/SCL pins
  Serial.begin(115200);

  while (!Serial) delay(10);  // Wait for serial
  Serial.setDebugOutput(true);
  Serial.println();

  Serial.println("-- Full Sense Board Test --"); Serial.println("");

  imu_func.init();
  Serial.println("IMU init done");

  pinMode(ledPin, OUTPUT);
  pinMode(led_pin1, OUTPUT);
  pinMode(led_pin2, OUTPUT);
  digitalWrite(ledPin, HIGH);  // turn the LED on (HIGH is the voltage level)
  delay(1000);

  myServo1.attach(servoPin1, 750, 2250);  // Attach the servo to the specified pin
  delay(1000);
  myServo2.attach(servoPin2, 750, 2250);  // Attach the servo to the specified pin

  Serial.println( "   Heap: " );
  Serial.print( "      Total: " );
  Serial.println( ESP.getHeapSize() );
  Serial.print( "      Used: " );
  Serial.println( ESP.getHeapSize() - ESP.getFreeHeap() );
  Serial.print( "      Free: " );
  Serial.println( ESP.getFreeHeap() );
  Serial.println( "   PSRAM: " );
  Serial.print( "      Total: " );
  Serial.println( ESP.getPsramSize() );
  Serial.print( "      Used: " );
  Serial.println( ESP.getPsramSize() - ESP.getFreePsram() );
  Serial.print( "      Free: " );
  Serial.println( ESP.getFreePsram() );

  camera_config_t config;
  config.ledc_channel = LEDC_CHANNEL_0;
  config.ledc_timer = LEDC_TIMER_0;
  config.pin_d0 = Y2_GPIO_NUM;
  config.pin_d1 = Y3_GPIO_NUM;
  config.pin_d2 = Y4_GPIO_NUM;
  config.pin_d3 = Y5_GPIO_NUM;
  config.pin_d4 = Y6_GPIO_NUM;
  config.pin_d5 = Y7_GPIO_NUM;
  config.pin_d6 = Y8_GPIO_NUM;
  config.pin_d7 = Y9_GPIO_NUM;
  config.pin_xclk = XCLK_GPIO_NUM;
  config.pin_pclk = PCLK_GPIO_NUM;
  config.pin_vsync = VSYNC_GPIO_NUM;
  config.pin_href = HREF_GPIO_NUM;
  config.pin_sccb_sda = SIOD_GPIO_NUM;
  config.pin_sccb_scl = SIOC_GPIO_NUM;
  config.pin_pwdn = PWDN_GPIO_NUM;
  config.pin_reset = RESET_GPIO_NUM;
  config.xclk_freq_hz = 20000000;
  config.frame_size = FRAMESIZE_UXGA;
  config.pixel_format = PIXFORMAT_JPEG;  // for streaming
  //config.pixel_format = PIXFORMAT_RGB565; // for face detection/recognition
  config.grab_mode = CAMERA_GRAB_WHEN_EMPTY;
  config.fb_location = CAMERA_FB_IN_PSRAM;
  config.jpeg_quality = 12;
  config.fb_count = 1;

  // if PSRAM IC present, init with UXGA resolution and higher JPEG quality
  //                      for larger pre-allocated frame buffer.
  if (config.pixel_format == PIXFORMAT_JPEG) {
    if (psramFound()) {
      config.jpeg_quality = 10;
      config.fb_count = 2;
      config.grab_mode = CAMERA_GRAB_LATEST;
    } else {
      // Limit the frame size when PSRAM is not available
      config.frame_size = FRAMESIZE_SVGA;
      config.fb_location = CAMERA_FB_IN_DRAM;
    }
  } else {
    // Best option for face detection/recognition
    config.frame_size = FRAMESIZE_240X240;
#if CONFIG_IDF_TARGET_ESP32S3
    config.fb_count = 2;
#endif
  }

#if defined(CAMERA_MODEL_ESP_EYE)
  pinMode(13, INPUT_PULLUP);
  pinMode(14, INPUT_PULLUP);
#endif
  

  // camera init
  esp_err_t err = esp_camera_init(&config);
  if (err != ESP_OK) {
    Serial.printf("Camera init failed with error 0x%x", err);
    // return;
    delay(1000);
  }

  sensor_t *s = esp_camera_sensor_get();
  // initial sensors are flipped vertically and colors are a bit saturated
  if (s->id.PID == OV3660_PID) {
    s->set_vflip(s, 1);        // flip it back
    s->set_brightness(s, 1);   // up the brightness just a bit
    s->set_saturation(s, -2);  // lower the saturation
  }
  // drop down frame size for higher initial frame rate
  if (config.pixel_format == PIXFORMAT_JPEG) {
    s->set_framesize(s, FRAMESIZE_QVGA);
  }

#if defined(CAMERA_MODEL_M5STACK_WIDE) || defined(CAMERA_MODEL_M5STACK_ESP32CAM)
  s->set_vflip(s, 1);
  s->set_hmirror(s, 1);
#endif

#if defined(CAMERA_MODEL_ESP32S3_EYE)
  s->set_vflip(s, 1);
#endif

// Setup LED FLash if LED pin is defined in camera_pins.h
#if defined(LED_GPIO_NUM)
  setupLedFlash(LED_GPIO_NUM);
#endif

  WiFi.begin(ssid, password);
  WiFi.setSleep(false);

  while (WiFi.status() != WL_CONNECTED) {
    delay(500);
    Serial.print(".");
  }
  WiFi.onEvent(WiFiEvent);
  Serial.println("");
  Serial.println("WiFi connected");
  Serial.print("IP Address: ");
  Serial.println(WiFi.localIP());

  startCameraServer();

  Serial.print("Camera Ready! Use 'http://");
  Serial.print(WiFi.localIP());
  Serial.println("' to connect");
}

void loop() {
  imu_func.update();
  delay(1000);
  digitalWrite(ledPin, ledState);  // turn the LED on (HIGH is the voltage level)
  ledState = ~ledState;
  Serial.print("LED State");
  Serial.println(led_pin_state);
  digitalWrite(led_pin1, 1);
  delay(10);
  digitalWrite(led_pin2, led_pin_state);
  delay(10);
  Serial.print("Camera Ready! Use 'http://");
  Serial.print(WiFi.localIP());
  Serial.println("' to connect");
}

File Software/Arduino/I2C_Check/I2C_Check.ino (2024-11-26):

#include <Wire.h>
 
void setup() {
  Wire.begin(45, 44);
  Serial.begin(115200);
  Serial.println("\nI2C Scanner");
}
 
void loop() {
  byte error, address;
  int nDevices;
  Serial.println("Scanning...");
  nDevices = 0;
  for(address = 1; address < 127; address++ ) {
    Wire.beginTransmission(address);
    error = Wire.endTransmission();
    if (error == 0) {
      Serial.print("I2C device found at address 0x");
      if (address<16) {
        Serial.print("0");
      }
      Serial.println(address,HEX);
      nDevices++;
    }
    else if (error==4) {
      Serial.print("Unknow error at address 0x");
      if (address<16) {
        Serial.print("0");
      }
      Serial.println(address,HEX);
    }    
  }
  if (nDevices == 0) {
    Serial.println("No I2C devices found\n");
  }
  else {
    Serial.println("done\n");
  }
  delay(5000);          
}

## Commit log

2024-09-30 initializing new sensing board folder/kicad project
    [SensingBoard_rev1.1.kicad_pcb, SensingBoard_rev1.1.kicad_sch]
2024-10-02 added datasheets, began schematic + component placement
    [SensingBoard_rev1.1.kicad_pcb, SensingBoard_rev1.1.kicad_sch, XIAO ESP32C3.brd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]
2024-10-02 more component placement
    [SensingBoard_rev1.1.kicad_pcb, SensingBoard_rev1.1.kicad_sch]
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2024-10-03 poe board files made
    taken from datasheets from oilmex, working on redoing layout
    [ESP32-PoE_Rev_L1-BOM(WROOM) .ods, ESP32-PoE_Rev_L1-BOM(WROVER).ods, ESP32-PoE_Rev_L1.kicad_pcb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]
2024-10-04 add BNO055
    [Adafruit BNO055 STEMMA QT.brd, Adafruit BNO055 STEMMA QT.sch, Adafruit BNO055.brd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]
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2024-10-07 updated boards
    front outside circuit now split into 2 boards
    [PowerBoard_rev1.1.kicad_pcb, PowerBoard_rev1.1.kicad_sch, SensingBoard_rev1.1.kicad_pcb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]
2024-10-07 new block diagrams
    [ESP32-PoE_Rev_L1_v1.2.kicad_sch]
2024-10-09 finished power board
    [PowerBoard_rev1.1.kicad_pcb, PowerBoard_rev1.1.kicad_sch, SensingBoard_rev1.1.kicad_pcb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]
2024-10-09 fixing POE board symbols + circuit
    [ESP32-PoE_Rev_L1_v1.2.kicad_pcb, ESP32-PoE_Rev_L1_v1.2.kicad_sch, PowerBoard_rev1.1.kicad_pcb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]
2024-10-11 fixing ethernet and poe power circuits
    [ESP32-PoE_Rev_L1_v1.2.kicad_pcb, ESP32-PoE_Rev_L1_v1.2.kicad_sch]
2024-10-14 finished ESP for POE board
    [ESP32-PoE_Rev_L1_v1.2.kicad_sch]
2024-10-14 POE board partitioning
    [ESP32-PoE_Rev_L1_1.3a.kicad_pcb, ESP32-PoE_Rev_L1_1.3a.kicad_sch, ESP32-PoE_Rev_L1_1.3a.sch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]
2024-10-14 sense board
    [SensingBoard_rev1.1.kicad_pcb, SensingBoard_rev1.1.kicad_sch]
2024-10-14 completed sense board
    [SensingBoard_rev1.1.kicad_pcb, SensingBoard_rev1.1.kicad_sch]
2024-10-14 board edges
    [ESP32-PoE_Rev_L1_1.3a.kicad_pcb, ESP32-PoE_Rev_L1_1.3a.kicad_sch, ESP32_POE_rev1.3b.kicad_pcb]
2024-10-17 power board layout
    [PowerBoard_rev1.1.kicad_pcb, PowerBoard_rev1.1.kicad_sch, SensingBoard_rev1.1.kicad_sch]
2024-10-17 group b2b
    [PowerBoard_rev1.1.kicad_pcb]
2024-10-17 POE1 board
    [ESP32-PoE_Rev_L1_1.3a.kicad_pcb, ESP32-PoE_Rev_L1_1.3a.kicad_sch, PowerBoard_rev1.1.kicad_pcb]
2024-10-18 POE 2 board
    [ESP32_POE_rev1.3b.kicad_pcb, ESP32_POE_rev1.3b.kicad_sch]
2024-10-18 updated power
    finished swapping power board bulk cap, new POE board schematic
    [ESP32-PoE-ISO_Rev_K.kicad_pcb, ESP32-PoE-ISO_Rev_K.kicad_sch, ESP32-PoE-ISO_Rev_K.sch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]
2024-10-18 updated combined POE schematic
    [ESP32-PoE-ISO_Rev_K.kicad_pcb, ESP32-PoE-ISO_Rev_K.kicad_sch]
2024-10-18 split into 1.4a and b
    [ESP_POE_1.4a.kicad_pcb, ESP_POE_1.4a.kicad_sch, ESP_POE_1.4a.sch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]
2024-10-19 starting POE1 route
    [ESP32-PoE-ISO_Rev_K.kicad_pcb, ESP_POE_1.4a.kicad_pcb, ESP_POE_1.4a.kicad_sch]
2024-10-20 some bom on power out
    [PowerBoard_rev1.1.kicad_sch]
2024-10-20 power board out BOM
    [PowerBoard_rev1.1.kicad_sch]
2024-10-20 POE2 layout
    [ESP_POE_1.4b.kicad_pcb, ESP_POE_1.4b.kicad_sch]
2024-10-21 fixing DRC
    [ESP_POE_1.4a.kicad_pcb, ESP_POE_1.4a.kicad_sch, ESP_POE_1.4b.kicad_pcb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]
2024-10-21 updated power
    [PowerBoard_rev1.1.kicad_pcb]
2024-10-21 POE 1 passes
    [ESP_POE_1.4a.kicad_pcb, ESP_POE_1.4a.kicad_sch, ESP_POE_1.4b.kicad_pcb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]
2024-10-21 POE 2 passes DRC
    [ESP_POE_1.4b.kicad_pcb]
2024-10-22 1.4a half bom
    [ESP_POE_1.4a.kicad_pcb, ESP_POE_1.4a.kicad_sch, PowerBoard_rev1.1.kicad_sch]
2024-10-22 updated L
    [ESP_POE_1.4a.kicad_pcb]
2024-10-22 some bom
    [ESP_POE_1.4a.kicad_sch]
2024-10-22 just made it so we can...
    [ESP_POE_1.4a.kicad_pcb]
2024-10-22 POE 1.4a BOM Done
    [ESP_POE_1.4a.kicad_sch]
2024-10-22 temp save
    [ESP_POE_1.4a.csv, ESP_POE_1.4a.kicad_pcb, ESP_POE_1.4b.kicad_sch]
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2024-10-22 fixed 1.4a
    [ESP_POE_1.4a.kicad_pcb, ESP_POE_1.4a.kicad_sch, ESP_POE_1.4b.kicad_pcb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]
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2024-10-24 1.4a and 1.4b ready to fab
    [BOM_ESP_POE_1.4b.csv, BOM_ESP_POE_1.4b_jlc.csv, BOM_PowerBoard_rev1.1_jlc.csv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]
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2024-10-28 update sensing board bom
    [SensingBoard_rev1.1.kicad_sch]
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2024-11-09 Improve performance with external oscillator EVB board
    [ethernet_example_main.c]
2024-11-13 Added cam webserver code
    [partitions.csv]
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2024-11-27 Added SDA/SCL pin fix
    [CameraWebServer.ino]
2024-12-19 Some debug fixes for sense dev board
    [CameraWebServer.ino, FULLAP_Test.ino]
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2025-01-30 schematic for v2.1 dev board done. Footprints update progress. Layout will roll when footprints finalize
    [InnerBoard_rev2.1.kicad_pcb, InnerBoard_rev2.1.kicad_sch]
2025-02-02 Inner board 2.1 footprint links fixed (for future work) and more included. Layout will roll when footprints finalize
    [InnerBoard_rev2.1.kicad_sch, OuterBoard_rev2.1.kicad_sch]
2025-02-02 Inner board 2.1 footprint links refactored (for future work) and more included. Layout will roll when footprints finalize
    [InnerBoard_rev2.1.kicad_sch]
2025-02-05 Inner board 2.1 footprint links refactored (for future work) and added all links. Routing progress
    [InnerBoard_rev2.1.kicad_pcb, InnerBoard_rev2.1.kicad_sch, MCP100-270DI_TO.step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]
2025-02-05 Routing progress. Mergedf 3.3v and 3v3
    [InnerBoard_rev2.1.kicad_pcb, InnerBoard_rev2.1.kicad_sch]
2025-02-05 Routing progress. Team meeting lead us to notice discrepancy. Dev board now in the hands of Rohan and Yimeng!
    [InnerBoard_rev2.1.kicad_pcb, InnerBoard_rev2.1.kicad_sch]
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2025-02-06 footprints on buttons
    stuff
    [ESP32-PoE-ISO_Rev_K.kicad_sch]
2025-02-12 fix lib
    [ECS-120-20-33-CKM-TR3.step, ESP32-PoE-ISO_Rev_K.kicad_pcb, ESP32-PoE-ISO_Rev_K.kicad_sch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]
2025-02-16 wait for testing result
    [ESP32-PoE-ISO_Rev_K.kicad_pcb, ESP32-PoE-ISO_Rev_K.kicad_sch, OuterBoard_rev3.1.kicad_sch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]
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2025-03-10 Fixed motor functionality for ov5640 cam
    [app_httpd.cpp]
2025-03-14 Fix documentation and motor pin
    [partitions.csv]
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2025-05-05 updated BOM and Fab
    [2024-11-19T193146.xlsx, JLC_OuterBoard_4.1.xlsx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]
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2025-07-25 tip-sensing board v4.2 upload
    [5051102491.step, 6130XX11121_61300611121.step, 87224-1.step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]
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2025-07-25 cleaned up outerboard4.2 folder
    [5051102491.step, 6130XX11121_61300611121.step, 87224-1.step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]
2025-08-09 updated fab file for board4.2
    [jlcpcb_OuterBoard_4.2_bom.csv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]
2025-10-24 add .gitignore for Kicad backups
    [BOM_ESP_POE_1.4a.csv, BOM_ESP_POE_1.4a_jlc.csv, BOM_ESP_POE_1.4b.csv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]

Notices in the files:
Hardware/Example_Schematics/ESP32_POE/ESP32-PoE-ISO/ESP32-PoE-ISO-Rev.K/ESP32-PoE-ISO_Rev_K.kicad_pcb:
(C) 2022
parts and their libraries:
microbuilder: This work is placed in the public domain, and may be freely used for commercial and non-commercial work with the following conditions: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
